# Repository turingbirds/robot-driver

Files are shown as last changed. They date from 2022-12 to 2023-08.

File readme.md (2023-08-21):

# Robot driver

Heavy duty 12 V servo motor driver with Wifi link

**⚠️ Status: prototype ⚠️**

https://user-images.githubusercontent.com/1014092/205401948-c3db500c-c33b-486b-9b15-0c6e07ba4ee2.mp4

pcb

rear

## Features

- 3 bidirectional motor outputs (motors wired as H-bridge; 6 output channels in total)
- Wireless low-latency interface via UDP
- Battery powered with a 14.4 V Makita power tool battery
- Flexible I/O options for motor position encoders, servo motor drivers, etc.
- Hardware address pins allow multiple devices on a network
- Unity VR interface

## Tech

- ESP32 controller
- BTS7960 driver for each output channel
- Inrush current limiter via low-side series MOSFET

PCB fits the case of a Makita battery charger.

Bill of materials: [CSV](bom.csv)

## Benchmarking

### Motor driver

Supply rail transient response during the demo program (as in the video):

transients

transients2

### Network

Each controller announces its presence by sending a UDP broadcast message containing its hardware address and IP address.

Packets containing control commands can then sent to a specific IP address, based on selecting a hardware address.

#### UDP network benchmarks for uncongested wifi
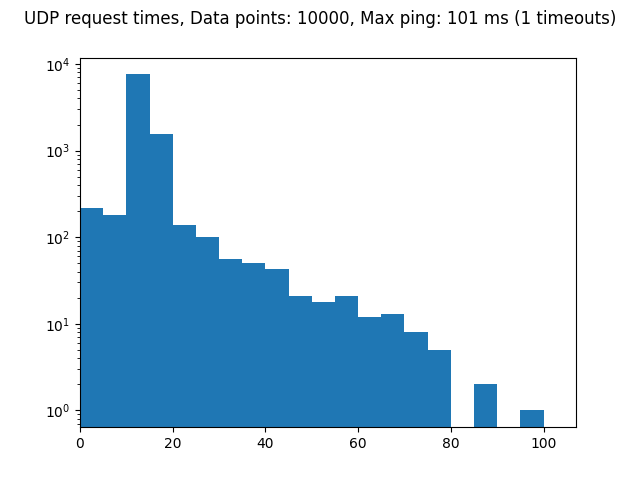
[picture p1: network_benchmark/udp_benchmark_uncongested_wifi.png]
Uncongested wifi


#### UDP network benchmarks for congested wifi
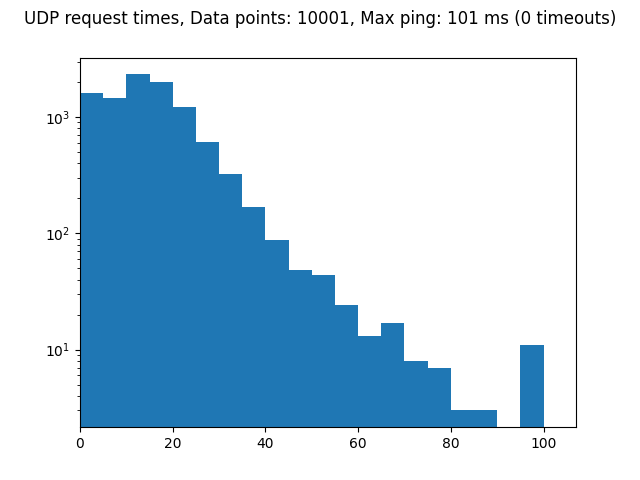
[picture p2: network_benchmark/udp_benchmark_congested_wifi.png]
Congested wifi


## License

[Open source hardware](https://www.oshwa.org/) is hardware for which the design is made publicly available, so that anyone can study, modify, distribute, make, and sell the design or hardware based on that design, subject to the following license conditions.

Hardware licensed under the *CERN Open Hardware Licence Version 2 - Weakly Reciprocal,* a copy of which is included in this repository at [cern_ohl_w_v2.txt](https://github.com/turingbirds/robot-driver/blob/master/cern_ohl_w_v2.txt).

Software licensed under the *Apache License 2.0,* a copy of which is included at [apache_license_2.0.txt](https://github.com/turingbirds/robot-driver/blob/master/apache_license_2.0.txt).

## Credits

This project was co-produced by V2_ Lab for the Unstable Media as part of the Winter Sessions art and technology residencies. ♥️

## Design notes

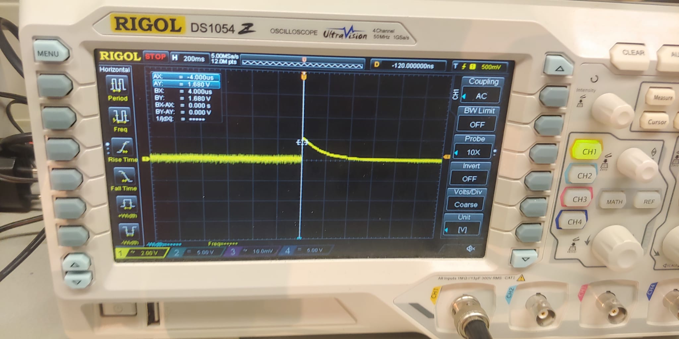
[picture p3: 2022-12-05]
doc/transients2.jpg

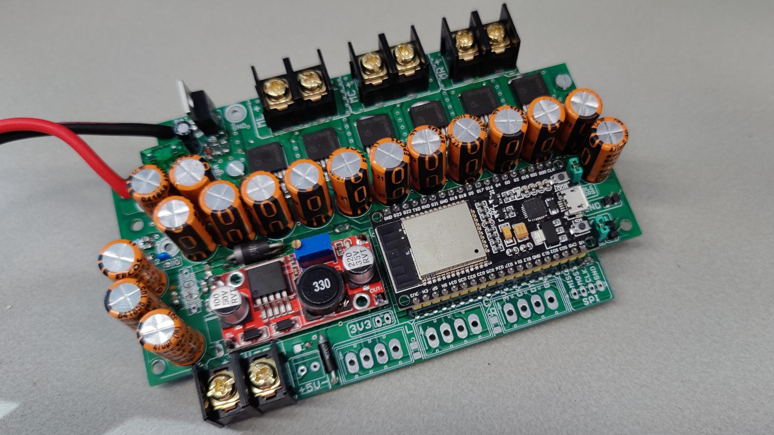
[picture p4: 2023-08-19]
doc/pcb.jpeg

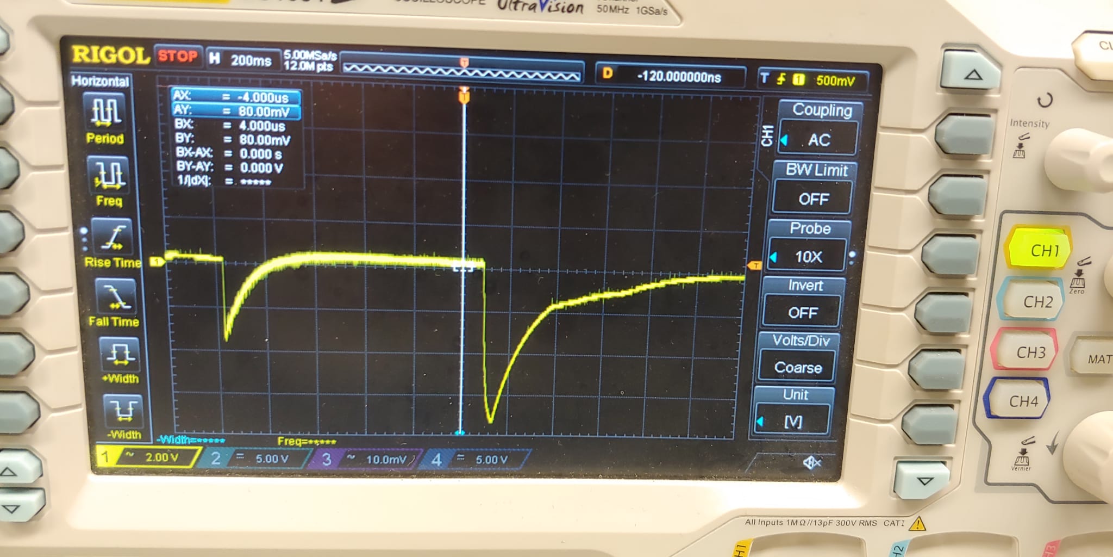
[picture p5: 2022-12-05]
doc/transients.jpg

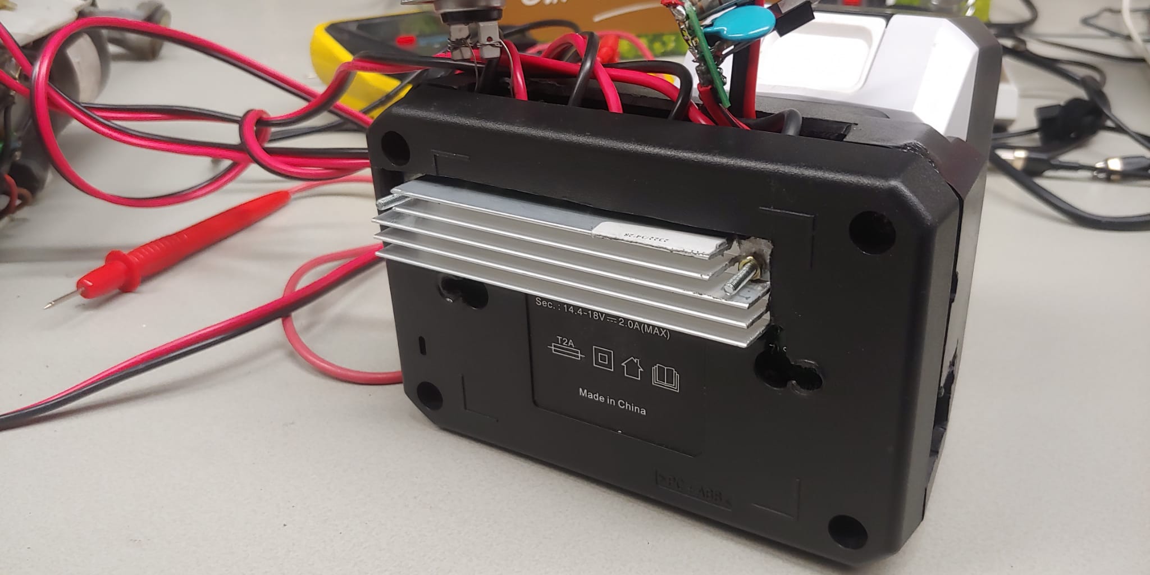
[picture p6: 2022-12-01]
doc/rear.jpeg

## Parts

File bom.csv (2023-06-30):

Qty | Identifier | Description | Value | Package | Price/1 | Price (tot)
6 | R1, R2, R3, R4, R5, R6 | Resistor 0 Ohm |  | 1206 | 0.05
8 | R7, R8, R9, R10, R11, R12, R13, R17 | Resistor 5k Ohm |  | 1206 | 0.05
1 | R14 | Resistor 100k Ohm |  | 1206 | 0.05
2 | R15, R19 | Resistor 100 Ohm 1 W |  | through-hole | 0.25
1 | R16 | Resistor 10k Ohm |  | 1206 | 0.05
1 | R18 | Resistor 22k Ohm |  | 1206 | 0.05
1 | R20 | Resistor 1.2k Ohm |  | 1206 | 0.05
1 | C41 | Electrolytic capacitor | 1 uF, 63V | through-hole, E2.5-6 | 0.25
2 | C1, C44 | Ceramic capacitor | 10 nF, 63 V | through-hole | 0.25
14 | C2, C3, C4, C5, C7, C8, C11, C12, C13, C16, C17, C19, C21, C24, C35, C36, C43 | Electrolytic capacitor | 470 uF, 35 V | through-hole, E5-10.5 | 0.68 | 9.47
23 | C6, C9, C10, C14, C15, C18, C22, C23, C25, C26, C27, C28, C29, C30, C31, C32, C33, C34, C37, C38, C39, C40, C42 | Ceramic capacitor (MLCC) | 100 nF, 25 V | 1206 | 0.05
1 | L1 | EMI suppression inductor (optional)
1 | D1 | 5V6 zener diode | 1N5339 | DO41 | 0.3 | 0.3
1 | D2, D6 | Schottky diode |  | DO15-12
1 | D3 | Schottky diode |  | DO214
2 | D4, D7 | TVS diode | P6KE22A | DO41-7.6 | 0.49 | 0.98
1 | SV6 | IDC header 4-pin
3 | SV7, SV8, SV9 | Screw terminals 4 mm pitch |  |  | 0.12 | 0.36
4 | X1, X6, X7, X8 | Screw terminals 10 mm pitch |  |  | 0.18 | 0.72
1 |  | jumper
3 | JP1, JP2, JP3 | IDC header 2-pin
1 |  | Socket for ESP32 (2x 19 pin female IDC)
 | J6 | Header (optional)
1 | IC2 | ESP32-DEVKIT |  |  | 5 | 5
1 | Q1 | IRLB8743 n-MOSFET |  | TO220 | 3.92 | 3.92
6 | IC3, IC4, IC5, IC6, IC7, IC8 | BTS7960B |  | TO263-7 | 1.44 | 8.62
1 | SV1 | 5V buck converter |  |  | 0.8 | 0.8
1 |  | Heatsink 20x108 mm |  |  | 0.75 | 0.75
1 |  | Thermal pad 20x108 mm |  |  | 2.33 | 2.33
1 |  | 5V DC fan 20 or 25 mm (optional)
1 | F2 | Mini car fuse + holder |  |  | 0.15 | 0.15
1 |  | Enclosure

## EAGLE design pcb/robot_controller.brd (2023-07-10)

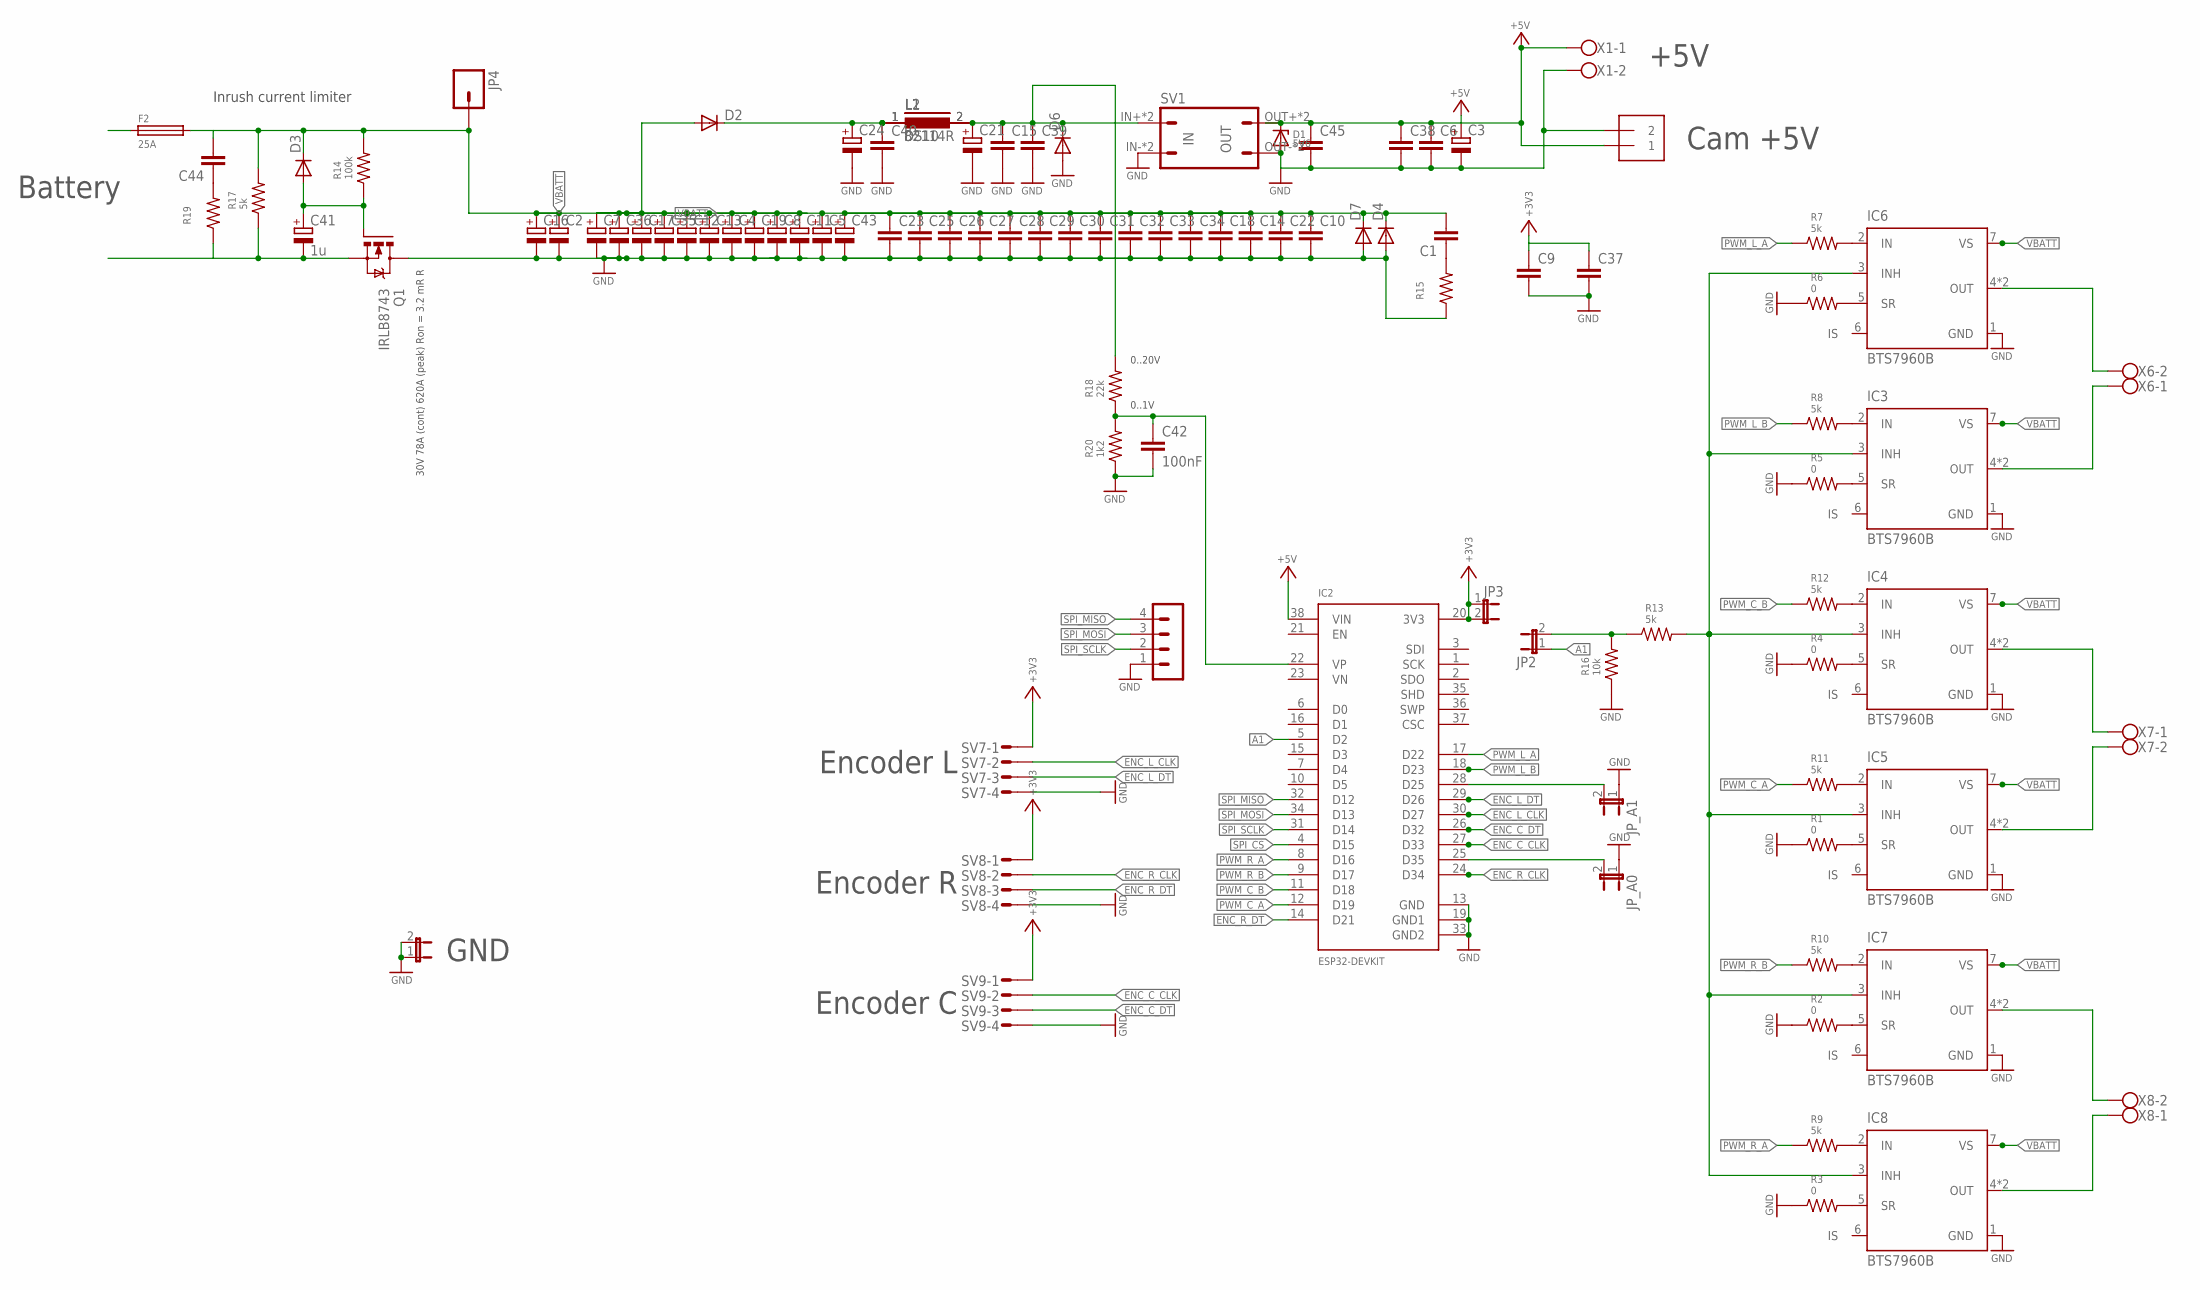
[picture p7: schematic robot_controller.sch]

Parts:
C1: C-EU025-025X050; C025-025X050
C2, C3, C4, C5, C7, C8, C11, C12, C13, C16, C17, C19, C21, C24, C35, C36, C43: CPOL-EUE5-10.5; E5-10,5
C6, C9, C10, C14, C15, C18, C22, C23, C25, C26, C27, C28, C29, C30, C31, C32, C33, C34, C37, C38, C39, C40, C45: C-EUC1206; C1206
C41: 1u; E2,5-6
C42: 100nF; C1206
C44: C-EU050-030X075; C050-030X075
D1: 5V6; DO41Z10
D2, D6: DIODE-DO15-12; DO15-12
D3: DIODE-DO-214AC; DO-214AC
D4, D7: DIODE-DO41-7.6; DO41-7.6
F2: 25A; SHK20L
IC2: ESP32-DEVKIT; DEVKIT-V1-NOHOLES
IC3, IC4, IC5, IC6, IC7, IC8: BTS7960B; P-TO263-7-1
J6: 1X2-3.5MM; 3.5MMTERM
JP1, JP2, JP3: JP1E; JP1
JP4: M01PTH_LONGPAD; 1X01_LONGPAD
JP_A0, JP_A1: JP1E; JP1
L1: 82114R
L2: DS10
Q1: IRLB8743; TO220BV
R1, R2, R3, R4, R5, R6: 0; R1206
R7, R8, R9, R10, R11, R12, R13, R17: 5k; R1206
R14: 100k; R1206
R15: R-US_0411/3V; 0411V
R16: 10k; R1206
R18: 22k; R1206
R19: R-US_0617/5V; 0617V
R20: 1k2; R1206
SV1: MA04-1SMALL; MA04-2
SV6: MA04-1
SV7, SV8, SV9: MT6-4
X1, X6, X7, X8: W239-302

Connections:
+3V3: C9.1, C37.1, IC2.20 (3V3), JP3.1, JP3.2, SV7.1, SV8.1, SV9.1
+5V: C3.+, C6.1, C38.1, C45.1, D1.C, IC2.38 (VIN), J6.1, SV1.OUT+, SV1.OUT+1 (OUT+), X1.1
A1: IC2.5 (D2), JP2.1
ENC_C_CLK: IC2.27 (D33), SV9.2
ENC_C_DT: IC2.26 (D32), SV9.3
ENC_L_CLK: IC2.30 (D27), SV7.2
ENC_L_DT: IC2.29 (D26), SV7.3
ENC_R_CLK: IC2.24 (D34), SV8.2
ENC_R_DT: IC2.14 (D21), SV8.3
GND: C2.-, C3.-, C4.-, C5.-, C6.2, C7.-, C8.-, C9.2, C10.2, C11.-, C12.-, C13.-, C14.2, C15.2, C16.-, C17.-, C18.2, C19.-, C21.-, C22.2, C23.2, C24.-, C25.2, C26.2, C27.2, C28.2, C29.2, C30.2, C31.2, C32.2, C33.2, C34.2, C35.-, C36.-, C37.2, C38.2, C39.2, C40.2, C42.2, C43.-, C45.2, D1.A, D4.A, D6.A, D7.A, IC2.13 (GND), IC2.19 (GND1), IC2.33 (GND2), IC3.1 (GND), IC4.1 (GND), IC5.1 (GND), IC6.1 (GND), IC7.1 (GND), IC8.1 (GND), J6.2, JP1.1, JP1.2, JP_A0.1, JP_A1.1, Q1.D, R1.1, R2.1, R3.1, R4.1, R5.1, R6.1, R15.1, R16.1, R20.1, SV1.IN-, SV1.IN-1 (IN-), SV1.OUT-, SV1.OUT-1 (OUT-), SV6.1, SV7.4, SV8.4, SV9.4, X1.2
unnamed: C24.+, C40.1, D2.C, L1.1, L2.1
unnamed: IC7.4 (OUT), IC7.8 (OUT), X8.2
unnamed: IC7.5 (SR), R2.2
unnamed: IC8.4 (OUT), IC8.8 (OUT), X8.1
unnamed: IC5.4 (OUT), IC5.8 (OUT), X7.2
unnamed: IC4.4 (OUT), IC4.8 (OUT), X7.1
unnamed: F2.1A (1), F2.1B (1)
unnamed: IC2.28 (D25), JP_A1.2
unnamed: IC3.4 (OUT), IC3.8 (OUT), X6.1
unnamed: IC6.4 (OUT), IC6.8 (OUT), X6.2
unnamed: IC5.5 (SR), R1.2
unnamed: IC8.5 (SR), R3.2
unnamed: IC4.5 (SR), R4.2
unnamed: C15.1, C21.+, C39.1, D6.C, L1.2, L2.2, R18.2, SV1.IN+, SV1.IN+1 (IN+)
unnamed: IC3.5 (SR), R5.2
unnamed: IC6.5 (SR), R6.2
unnamed: IC3.3 (INH), IC4.3 (INH), IC5.3 (INH), IC6.3 (INH), IC7.3 (INH), IC8.3 (INH), R13.2
unnamed: IC6.2 (IN), R7.2
unnamed: IC4.2 (IN), R12.2
unnamed: IC5.2 (IN), R11.2
unnamed: IC7.2 (IN), R10.2
unnamed: IC8.2 (IN), R9.2
unnamed: IC3.2 (IN), R8.2
unnamed: C1.1, R15.2
unnamed: JP2.2, R13.1, R16.2
unnamed: IC2.25 (D35), JP_A0.2
unnamed: C41.+, D3.A, Q1.G, R14.1
unnamed: C41.-, Q1.S, R17.1, R19.1
unnamed: C42.1, IC2.22 (VP), R18.1, R20.2
unnamed: C44.1, R19.2
PWM_C_A: IC2.12 (D19), R11.1
PWM_C_B: IC2.11 (D18), R12.1
PWM_L_A: IC2.17 (D22), R7.1
PWM_L_B: IC2.18 (D23), R8.1
PWM_R_A: IC2.8 (D16), R9.1
PWM_R_B: IC2.9 (D17), R10.1
SPI_CS: IC2.4 (D15)
SPI_MISO: IC2.32 (D12), SV6.4
SPI_MOSI: IC2.34 (D13), SV6.3
SPI_SCLK: IC2.31 (D14), SV6.2
VBATT: C1.2, C2.+, C4.+, C5.+, C7.+, C8.+, C10.1, C11.+, C12.+, C13.+, C14.1, C16.+, C17.+, C18.1, C19.+, C22.1, C23.1, C25.1, C26.1, C27.1, C28.1, C29.1, C30.1, C31.1, C32.1, C33.1, C34.1, C35.+, C36.+, C43.+, C44.2, D2.A, D3.C, D4.C, D7.C, F2.2A (2), F2.2B (2), IC3.7 (VS), IC4.7 (VS), IC5.7 (VS), IC6.7 (VS), IC7.7 (VS), IC8.7 (VS), JP4.1, R14.2, R17.2

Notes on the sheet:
GND
Battery
Encoder L
Encoder R
Encoder C
Cam +5V
+5V
Inrush current limiter
30V 78A (cont) 620A (peak) Ron = 3.2 mR R
0..20V
0..1V

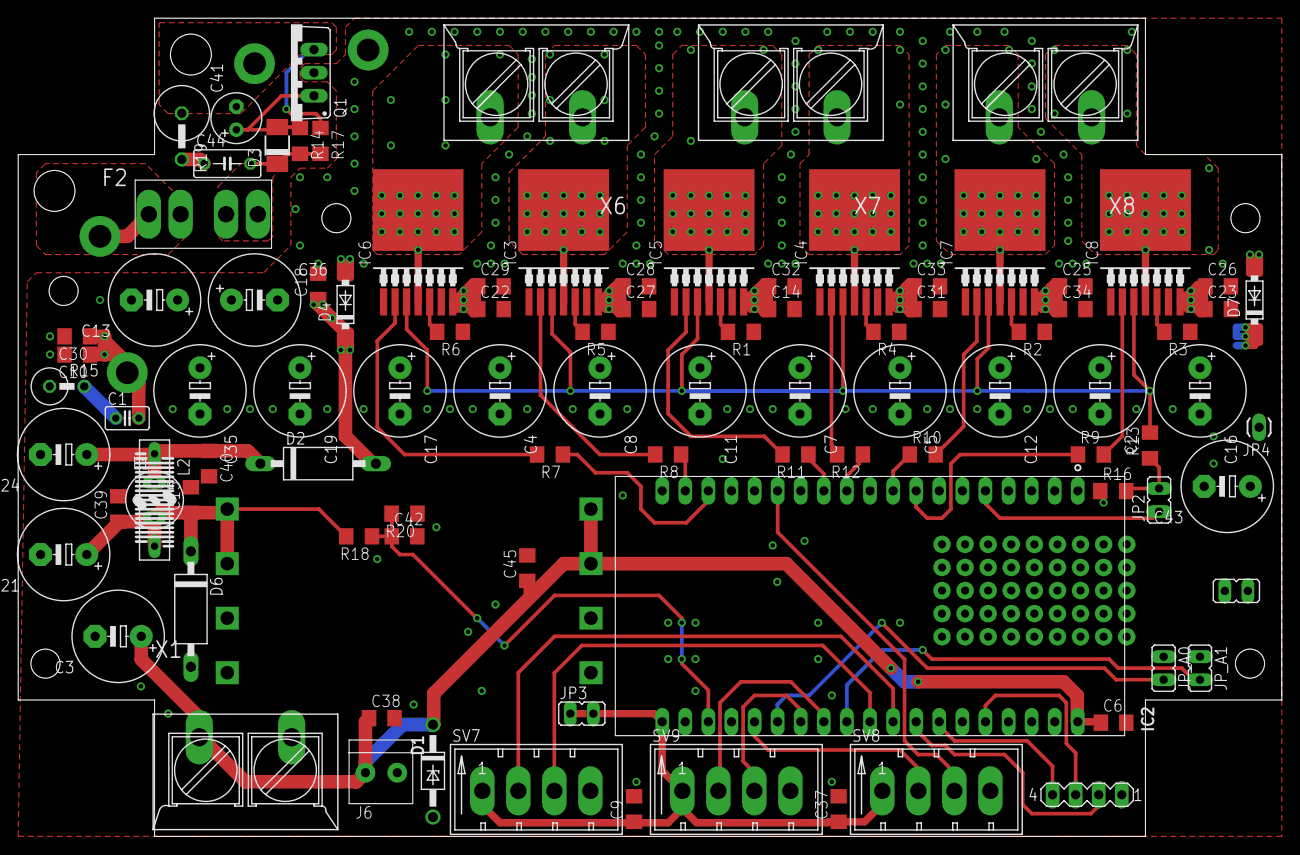
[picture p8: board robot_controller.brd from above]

Board: 2 copper layers, 139.0 x 90.0 mm, 97 parts (0 on the bottom side), 50 nets.

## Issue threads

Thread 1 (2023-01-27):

Add address selection jumpers/switches

turingbirds, 2023-01-27:
Add a feature to allow setting a unique address for each controller using a set of jumpers or switches on the PCB. This makes it easy to use multiple separate controllers at the same time without interference.

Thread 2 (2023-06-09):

Add timing benchmarks

turingbirds, 2023-06-09:
Work in progress.

[esp32_http_server_ping_benchmarks.zip](https://github.com/turingbirds/robot-driver/files/11710532/esp32_http_server_ping_benchmarks.zip)

turingbirds, 2023-06-11:
# HTTP request, uncongested wifi

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

# HTTP request, congested wifi

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

# UDP packet, uncongested wifi

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

# UDP packet, congested wifi

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

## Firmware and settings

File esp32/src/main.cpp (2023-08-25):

/*

Robot controller
----------------

https://github.com/turingbirds/robot-driver

Copyright 2023
Apache License 2.0

*/


/*
 * Serial debugging
**/

// warning!! Enabling serial debug will increase response latency
// set to 1 for on, 0 for off.
#define SERIAL_DEBUG 1
#define SERIAL_DEBUG_DETAILED 0

// broadcast our hardware and IP address over UDP?
#define UDP_BROADCAST 1

#include <esp_task_wdt.h>


/*
 * Wifi
**/

#define WIFI_SSID "wifi ssid"
#define WIFI_PSK  "wifi password"

#include <Esp.h>
#include "esp_system.h"
#include "esp_sleep.h"

#include <WiFi.h>
#include <ArduinoJson.h>
#include "AsyncUDP.h"


// demo mode: no wifi and MQTT, just pulse motors one after the other
#define DEMO_MODE 0
#define DEMO_MODE_ADC_READING 0

// use feedback encoders/servo mode for main motors
#define USE_ENCODERS 0

#define MEASURE_MOTOR_ABSOLUTE_ANGLE 1

// control small "normal" PWM servo motors (pins shared with encoder inputs--select only one at a time)
#define AUX_SERVO_CONTROLLER 1

#define MIN(x, y) ((x)<(y)?(x):(y))
#define MAX(x, y) ((x)>(y)?(x):(y))

// ----------------------------------------------------------------------------
// definitions

#define ADDRESS_SELECT_A0_PIN 35
#define ADDRESS_SELECT_A1_PIN 25

volatile size_t hardware_address = 0;

#define PWM_RESOLUTION 8
#define PWM_FREQ  25000

#define PWM_L_PIN_A 22
#define PWM_L_PIN_B 23
#define PWM_R_PIN_A 19
#define PWM_R_PIN_B 18
#define PWM_C_PIN_A 17
#define PWM_C_PIN_B 16

#define PWM_EN_PIN 2

#define MOTOR_L_PWM_CHANNEL_A 6
#define MOTOR_L_PWM_CHANNEL_B 7
#define MOTOR_R_PWM_CHANNEL_A 2
#define MOTOR_R_PWM_CHANNEL_B 3
#define MOTOR_C_PWM_CHANNEL_A 4
#define MOTOR_C_PWM_CHANNEL_B 5

#if USE_ENCODERS
#define ENCODER_L_CLK_PIN 27
#define ENCODER_L_DT_PIN 26
#define ENCODER_R_CLK_PIN 34
#define ENCODER_R_DT_PIN 21
#define ENCODER_C_CLK_PIN 33
#define ENCODER_C_DT_PIN 32
#endif

#if MEASURE_MOTOR_ABSOLUTE_ANGLE
#define MOTOR_L_ZERO_SWITCH_PIN 26
#define MOTOR_R_ZERO_SWITCH_PIN 34
#endif

#if AUX_SERVO_CONTROLLER
#define AUX_SERVO_PWM_FREQ     50
#define AUX_SERVO_PWM_RESOLUTION  8

#define AUX_SERVO_1_PIN 21
#define AUX_SERVO_2_PIN 33

#define AUX_SERVO_PWM_CHANNEL_1 0
#define AUX_SERVO_PWM_CHANNEL_2 1
#endif

#define BAT_VOLT_ADC_PIN 36

const unsigned int min_dutycycle = 30;  // allow transistor to turn fully on before turning it off on heavy loads (transistor spends too much time in linear range below this value)
const unsigned int max_dutycycle = 211;  // 14.4V supply for a 12V motor -> 83% max duty = 211/255. In the future this could be made dependent on measured battery voltage

// 3 seconds WDT
#define WDT_TIMEOUT 3

#if AUX_SERVO_CONTROLLER
#include <ESP32Servo.h>
#endif

#if !DEMO_MODE
WiFiClient espClient;
AsyncUDP udp;

volatile unsigned long prev_millis = 0;
const unsigned long WIFI_RECONNECT_INTERVAL = 5000; // in milliseconds

unsigned int udp_comms_timeout = 500; // timeout in milliseconds -- stop robot if no packets received for this interval or more
unsigned int udp_time_since_last_packet = 0;
#endif

// ----------------------------------------------------------------------------
// Global state

#if DEMO_MODE
volatile uint8_t foo = 0;
volatile uint8_t motor_idx = 0;
#endif

volatile unsigned int message_counter = 0;

volatile unsigned int frame = 0;

volatile uint32_t serial_delay_counter = 0;
// volatile uint32_t serial_delay_counter2 = 0;
volatile uint32_t bat_volt_adc_raw = 0;
volatile float bat_volt_adc_corrected = -1.;

volatile int vel_L = 0;
volatile int vel_R = 0;
volatile int vel_C = 0;

volatile unsigned int enable_L = 1;   // set to 0 to disable motor
volatile unsigned int enable_R = 1;   // set to 0 to disable motor

volatile unsigned int stop_motor_L_at_zero = 0; // set to 1 to activate
volatile unsigned int stop_motor_R_at_zero = 0; // set to 1 to activate

#if AUX_SERVO_CONTROLLER
// initial servo positions
volatile unsigned int aux_pos_1 = 90;
volatile unsigned int aux_pos_2 = 90;

const unsigned int MAX_AUX_POS_1 = 140;
const unsigned int MIN_AUX_POS_1 = 60;

Servo aux_servo_1;
Servo aux_servo_2;
#endif



//
// void IRAM_ATTR MOTOR_L_PIN_CHANGE_ISR() {
// 	if (stop_motor_L_at_zero) {
// 		enable_L = 0;
// 	}
// }
//
// void IRAM_ATTR MOTOR_R_PIN_CHANGE_ISR() {
// 	if (stop_motor_R_at_zero) {
// 		enable_R = 0;
// 	}
// }




void init_udp_listener() {
	if (udp.listen(1234)) {
		udp.onPacket([](AsyncUDPPacket packet) {

#if SERIAL_DEBUG
			Serial.print("[host -> esp32] UDP Packet Type: ");
			Serial.print(packet.isBroadcast() ? "Broadcast" : packet.isMulticast() ? "Multicast" : "Unicast");
			Serial.print(", From: ");
			Serial.print(packet.remoteIP());
			Serial.print(":");
			Serial.print(packet.remotePort());
			Serial.print(", To: ");
			Serial.print(packet.localIP());
			Serial.print(":");
			Serial.print(packet.localPort());
			Serial.print(", Length: ");
			Serial.print(packet.length()); //dlzka packetu
			Serial.print(", Data: ");
			Serial.write(packet.data(), packet.length());
			Serial.println();
#endif

			if (packet.isBroadcast()) return;

			// reset packet timeout
			udp_time_since_last_packet = 0;

			String data_as_string = (const char*)packet.data();
			DynamicJsonDocument doc(1024);
			deserializeJson(doc, data_as_string);
#if SERIAL_DEBUG
			// Serial.write("[[[]]]%f]]", doc["vel_L"]);


						// message_counter += 1;

				    // char s[256];
			//			sprintf(s, "{\"vel_L\": \"%d\", \"vel_C\": \"%d\", \"vel_R\": \"%d\", \"aux_pos_1\": \"%d\", \"aux_pos_2\": \"%d\", \"cnt\": \"%d\", \"battery_voltage\": \"%f\"}\0", vel_L, vel_C, vel_R, aux_pos_1, aux_pos_2, message_counter, bat_volt_adc_corrected);
						// sprintf(s, "{\"vel_L\": \"%d\", \"vel_C\": \"%d\", \"vel_R\": \"%d\", \"aux_pos_1\": \"%d\", \"aux_pos_2\": \"%d\", \"cnt\": \"%d\", \"battery_voltage\": \"%f\"}\0", vel_L, vel_C, vel_R, aux_pos_1, aux_pos_2, message_counter, bat_volt_adc_corrected);



#endif
			vel_L = doc["vel_L"];
			vel_C = doc["vel_C"];
			vel_R = doc["vel_R"];
			stop_motor_L_at_zero = doc["stop_motor_L_at_zero"];
			stop_motor_R_at_zero = doc["stop_motor_R_at_zero"];
			if (doc["enable_R"]) {
				enable_R = 1;
			}
			if (doc["enable_L"]) {
				enable_L = 1;
			}
#if AUX_SERVO_CONTROLLER
			unsigned int aux_pos_1_new = doc["aux_pos_1"];
			aux_pos_1_new = MIN(MAX_AUX_POS_1, aux_pos_1_new);
			aux_pos_1_new = MAX(MIN_AUX_POS_1, aux_pos_1_new);
			aux_pos_1 = aux_pos_1_new;
			aux_pos_2 = doc["aux_pos_2"];
#endif

			// packet.printf("[esp32 -> host] received %u bytes of data", packet.length());
			packet.printf("{\"battery_voltage\": %f, \"free_heap\": %d, \"sw_L\": %d, \"sw_R\": %d}", bat_volt_adc_corrected, ESP.getFreeHeap(),
			digitalRead(MOTOR_L_ZERO_SWITCH_PIN), digitalRead(MOTOR_R_ZERO_SWITCH_PIN));
		});
	}
}

void init_address_select() {
	pinMode(ADDRESS_SELECT_A0_PIN, INPUT_PULLUP);  // Set the pin as input
	pinMode(ADDRESS_SELECT_A1_PIN, INPUT_PULLUP);  // Set the pin as input
}

void read_address_select() {
	const size_t A_0 = digitalRead(ADDRESS_SELECT_A0_PIN);
	const size_t A_1 = digitalRead(ADDRESS_SELECT_A1_PIN);
	hardware_address = (1 - A_0) | ((1 - A_1) << 1);
}

void init_motors() {
  ledcSetup(MOTOR_L_PWM_CHANNEL_A, PWM_FREQ, PWM_RESOLUTION);
  ledcSetup(MOTOR_L_PWM_CHANNEL_B, PWM_FREQ, PWM_RESOLUTION);
  ledcSetup(MOTOR_R_PWM_CHANNEL_A, PWM_FREQ, PWM_RESOLUTION);
  ledcSetup(MOTOR_R_PWM_CHANNEL_B, PWM_FREQ, PWM_RESOLUTION);
  ledcSetup(MOTOR_C_PWM_CHANNEL_A, PWM_FREQ, PWM_RESOLUTION);
  ledcSetup(MOTOR_C_PWM_CHANNEL_B, PWM_FREQ, PWM_RESOLUTION);

  ledcAttachPin(PWM_L_PIN_A, MOTOR_L_PWM_CHANNEL_A);
  ledcAttachPin(PWM_L_PIN_B, MOTOR_L_PWM_CHANNEL_B);
  ledcAttachPin(PWM_R_PIN_A, MOTOR_R_PWM_CHANNEL_A);
  ledcAttachPin(PWM_R_PIN_B, MOTOR_R_PWM_CHANNEL_B);
  ledcAttachPin(PWM_C_PIN_A, MOTOR_C_PWM_CHANNEL_A);
  ledcAttachPin(PWM_C_PIN_B, MOTOR_C_PWM_CHANNEL_B);

  // enable
  pinMode(PWM_EN_PIN, OUTPUT);
  digitalWrite(PWM_EN_PIN, HIGH);
}

void setup() {
#if SERIAL_DEBUG
  	delay(2000);
  	Serial.begin(115200);

  	Serial.println("Setting up WDT");
  	esp_task_wdt_init(WDT_TIMEOUT, true);
  	esp_task_wdt_add(NULL);

  	// Connect to WiFi
  	Serial.println("Setting up WiFi");
#endif
		init_address_select();
		read_address_select();

		WiFi.setSleep(false);
	  WiFi.begin(WIFI_SSID, WIFI_PSK);
	  while (WiFi.status() != WL_CONNECTED) {
			esp_task_wdt_reset();
	    Serial.print(".");
	    delay(500);
	  }
	  Serial.print("Connected. IP=");
	  Serial.println(WiFi.localIP());
		WiFi.setSleep(false);
		Serial.print("CPU frequency: ");
		Serial.println(getCpuFrequencyMhz());

		// init ADC
	  adcAttachPin(BAT_VOLT_ADC_PIN);
	  analogSetPinAttenuation(BAT_VOLT_ADC_PIN, ADC_2_5db);    // The input voltage of ADC will be attenuated, extending the range of measurement to up to approx. 1100 mV. (1V input = ADC reading of 3722)

		// initialize and power on the motors
	  init_motors();

	// #if AUX_SERVO_CONTROLLER
	//   ledcSetup(AUX_SERVO_PWM_CHANNEL_1, AUX_SERVO_PWM_FREQ, AUX_SERVO_PWM_RESOLUTION);
	//   ledcSetup(AUX_SERVO_PWM_CHANNEL_2, AUX_SERVO_PWM_FREQ, AUX_SERVO_PWM_RESOLUTION);
	//
	//   ledcAttachPin(AUX_SERVO_1_PIN, AUX_SERVO_PWM_CHANNEL_1);
	//   ledcAttachPin(AUX_SERVO_2_PIN, AUX_SERVO_PWM_CHANNEL_2);
	// #endif

#if AUX_SERVO_CONTROLLER
	  ESP32PWM::allocateTimer(AUX_SERVO_PWM_CHANNEL_1);
	  ESP32PWM::allocateTimer(AUX_SERVO_PWM_CHANNEL_2);
	  aux_servo_1.setPeriodHertz(50); // [Hz]
	  aux_servo_2.setPeriodHertz(50); // [Hz]
	  aux_servo_1.attach(AUX_SERVO_1_PIN, 500, 2400);
	  aux_servo_2.attach(AUX_SERVO_2_PIN, 500, 2400);
#endif

  pinMode(MOTOR_L_ZERO_SWITCH_PIN, INPUT_PULLUP);  // Set the pin as input
	pinMode(MOTOR_R_ZERO_SWITCH_PIN, INPUT_PULLUP);  // Set the pin as input
	//attachInterrupt(MOTOR_L_ZERO_SWITCH_PIN, MOTOR_L_PIN_CHANGE_ISR, RISING);
	//attachInterrupt(MOTOR_R_ZERO_SWITCH_PIN, MOTOR_R_PIN_CHANGE_ISR, RISING);



	init_udp_listener();
}

#if DEMO_MODE
void demo_mode_loop() {
  ++foo;
  if (foo > max_dutycycle) {
    foo = min_dutycycle;
    ++motor_idx;
    if (motor_idx >= 12) {
      motor_idx = 0;
    }

#if DEMO_MODE_ADC_READING5
    bat_volt_adc_raw = analogRead(BAT_VOLT_ADC_PIN);
    const float bat_volt_adc = bat_volt_adc_raw * 0.0067;
    const float bat_volt_adc_corrected = bat_volt_adc + (20. - bat_volt_adc) / 20.; // some ad-hoc correction of the horrible ADC nonlinearity

    Serial.print(bat_volt_adc_raw);
    Serial.println();
    Serial.printf("%f\n", bat_volt_adc_corrected);
#endif
  }

  // one motor after the other
  if (motor_idx == 0) {
    ledcWrite(MOTOR_L_PWM_CHANNEL_A, foo);
    ledcWrite(MOTOR_L_PWM_CHANNEL_B, 0);
    ledcWrite(MOTOR_R_PWM_CHANNEL_A, 0);
    ledcWrite(MOTOR_R_PWM_CHANNEL_B, 0);
    ledcWrite(MOTOR_C_PWM_CHANNEL_A, 0);
    ledcWrite(MOTOR_C_PWM_CHANNEL_B, 0);
  }
  else if (motor_idx == 1) {
    ledcWrite(MOTOR_L_PWM_CHANNEL_A, 0);
    ledcWrite(MOTOR_L_PWM_CHANNEL_B, 0);
    ledcWrite(MOTOR_R_PWM_CHANNEL_A, foo);
    ledcWrite(MOTOR_R_PWM_CHANNEL_B, 0);
    ledcWrite(MOTOR_C_PWM_CHANNEL_A, 0);
    ledcWrite(MOTOR_C_PWM_CHANNEL_B, 0);
  }
  else if (motor_idx == 2) {
    ledcWrite(MOTOR_L_PWM_CHANNEL_A, 0);
    ledcWrite(MOTOR_L_PWM_CHANNEL_B, 0);
    ledcWrite(MOTOR_R_PWM_CHANNEL_A, 0);
    ledcWrite(MOTOR_R_PWM_CHANNEL_B, 0);
    ledcWrite(MOTOR_C_PWM_CHANNEL_A, foo);
    ledcWrite(MOTOR_C_PWM_CHANNEL_B, 0);
  }
  else if (motor_idx == 3) {
    ledcWrite(MOTOR_L_PWM_CHANNEL_A, 0);
    ledcWrite(MOTOR_L_PWM_CHANNEL_B, foo);
    ledcWrite(MOTOR_R_PWM_CHANNEL_A, 0);
    ledcWrite(MOTOR_R_PWM_CHANNEL_B, 0);
    ledcWrite(MOTOR_C_PWM_CHANNEL_A, 0);
    ledcWrite(MOTOR_C_PWM_CHANNEL_B, 0);
  }
  else if (motor_idx == 4) {
    ledcWrite(MOTOR_L_PWM_CHANNEL_A, 0);
    ledcWrite(MOTOR_L_PWM_CHANNEL_B, 0);
    ledcWrite(MOTOR_R_PWM_CHANNEL_A, 0);
    ledcWrite(MOTOR_R_PWM_CHANNEL_B, foo);
    ledcWrite(MOTOR_C_PWM_CHANNEL_A, 0);
    ledcWrite(MOTOR_C_PWM_CHANNEL_B, 0);
  }
  else if (motor_idx == 5) {
    ledcWrite(MOTOR_L_PWM_CHANNEL_A, 0);
    ledcWrite(MOTOR_L_PWM_CHANNEL_B, 0);
    ledcWrite(MOTOR_R_PWM_CHANNEL_A, 0);
    ledcWrite(MOTOR_R_PWM_CHANNEL_B, 0);
    ledcWrite(MOTOR_C_PWM_CHANNEL_A, 0);
    ledcWrite(MOTOR_C_PWM_CHANNEL_B, foo);
  }
  else if (motor_idx == 6) {
    ledcWrite(MOTOR_L_PWM_CHANNEL_A, 0);
    ledcWrite(MOTOR_L_PWM_CHANNEL_B, foo);
    ledcWrite(MOTOR_R_PWM_CHANNEL_A, 0);
    ledcWrite(MOTOR_R_PWM_CHANNEL_B, foo);
    ledcWrite(MOTOR_C_PWM_CHANNEL_A, 0);
    ledcWrite(MOTOR_C_PWM_CHANNEL_B, foo);
  }
  else if (motor_idx == 7) {
    ledcWrite(MOTOR_L_PWM_CHANNEL_A, foo);
    ledcWrite(MOTOR_L_PWM_CHANNEL_B, 0);
    ledcWrite(MOTOR_R_PWM_CHANNEL_A, foo);
    ledcWrite(MOTOR_R_PWM_CHANNEL_B, 0);
    ledcWrite(MOTOR_C_PWM_CHANNEL_A, foo);
    ledcWrite(MOTOR_C_PWM_CHANNEL_B, 0);
  }
  else if (motor_idx == 8) {
    ledcWrite(MOTOR_L_PWM_CHANNEL_A, 0);
    ledcWrite(MOTOR_L_PWM_CHANNEL_B, max_dutycycle-foo);
    ledcWrite(MOTOR_R_PWM_CHANNEL_A, 0);
    ledcWrite(MOTOR_R_PWM_CHANNEL_B, max_dutycycle-foo);
    ledcWrite(MOTOR_C_PWM_CHANNEL_A, 0);
    ledcWrite(MOTOR_C_PWM_CHANNEL_B, max_dutycycle-foo);
  }
  else if (motor_idx == 9) {
    ledcWrite(MOTOR_L_PWM_CHANNEL_A, max_dutycycle-foo);
    ledcWrite(MOTOR_L_PWM_CHANNEL_B, 0);
    ledcWrite(MOTOR_R_PWM_CHANNEL_A, max_dutycycle-foo);
    ledcWrite(MOTOR_R_PWM_CHANNEL_B, 0);
    ledcWrite(MOTOR_C_PWM_CHANNEL_A, max_dutycycle-foo);
    ledcWrite(MOTOR_C_PWM_CHANNEL_B, 0);
  }
  else if (motor_idx == 10 || motor_idx == 11) {
    ledcWrite(MOTOR_L_PWM_CHANNEL_A, max_dutycycle);
    ledcWrite(MOTOR_L_PWM_CHANNEL_B, 0);
    ledcWrite(MOTOR_R_PWM_CHANNEL_A, max_dutycycle);
    ledcWrite(MOTOR_R_PWM_CHANNEL_B, 0);
    ledcWrite(MOTOR_C_PWM_CHANNEL_A, max_dutycycle);
    ledcWrite(MOTOR_C_PWM_CHANNEL_B, 0);
  }
  delay(10);
}
#endif

volatile float motor_l_zero_switch_pin = 0.;
volatile float motor_r_zero_switch_pin = 0.;

void read_battery_voltage() {
	const float bat_volt_adc_raw = analogRead(BAT_VOLT_ADC_PIN);
	const float bat_volt_adc = bat_volt_adc_raw * 0.0067;
	bat_volt_adc_corrected = bat_volt_adc + (20. - bat_volt_adc) / 20.; // some ad-hoc correction of the horrible ADC nonlinearity
}

void loop() {
	// reset watchdog timer
	esp_task_wdt_reset();
	unsigned long current_millis = millis();

	// update this in loop() so we can change the address without having to reboot
	read_address_select();

	// read out the motor zero-degree indicator pin and stop the motor if necessary
	motor_r_zero_switch_pin = .5 * motor_r_zero_switch_pin + .5 * ((int)digitalRead(MOTOR_R_ZERO_SWITCH_PIN));
	if (stop_motor_R_at_zero && motor_r_zero_switch_pin > .9) {
		enable_R = 0;
	}

	motor_l_zero_switch_pin = .5 * motor_l_zero_switch_pin + .5 * ((int)digitalRead(MOTOR_L_ZERO_SWITCH_PIN));
	if (stop_motor_L_at_zero && motor_l_zero_switch_pin > .9) {
		enable_L = 0;
	}

#if DEMO_MODE
	demo_mode_loop();
	return;

#else

	if (WiFi.status() != WL_CONNECTED) {
		vel_L = 0;
		vel_C = 0;
		vel_R = 0;

		Serial.println("Wifi got disconnected! Attempting to reconnect...");

		WiFi.disconnect();
		WiFi.setSleep(false);
	  WiFi.begin(WIFI_SSID, WIFI_PSK);
	  while (WiFi.status() != WL_CONNECTED) {
			esp_task_wdt_reset();
	    Serial.print(".");
	    delay(500);
	  }
	  Serial.print("Connected. IP=");
	  Serial.println(WiFi.localIP());
		WiFi.setSleep(false);

		udp_time_since_last_packet = 0;
	}

	// network timeout handling
	delay(10); // do not make delay too low (or other code in loop() take too long), otherwise the estimate for udp_time_since_last_packet will be off by too much
	udp_time_since_last_packet += 10;

	if (udp_time_since_last_packet > udp_comms_timeout) {
		vel_L = 0;
		vel_C = 0;
		vel_R = 0;
	}

  // report on battery voltage
	++serial_delay_counter;
	if (serial_delay_counter >= 100) { // every 100 ms
		serial_delay_counter = 0;

#if UDP_BROADCAST
	// broadcast our presence
	char s[80];
	sprintf(s, "Robot A%d, IP: %s", hardware_address, WiFi.localIP().toString().c_str());
	udp.broadcast(s);
#endif

#if SERIAL_DEBUG
		Serial.print("Free heap: ");
		Serial.println(ESP.getFreeHeap());
		Serial.print("IP: ");
		Serial.println(WiFi.localIP());
#if SERIAL_DEBUG_DETAILED
  // enabling this renders everything very, very slow
  Serial.print("vel_R = ");
  Serial.print(vel_R);
  Serial.print(". vel_L = ");
  Serial.print(vel_L);
  Serial.print(", vel_C = ");
  Serial.print(vel_C);
  Serial.println();
#if AUX_SERVO_CONTROLLER
  Serial.print("aux_servo_pos_1 = ");
  Serial.print(aux_pos_1);
  Serial.print(", aux_servo_pos_2 = ");
  Serial.print(aux_pos_2);
  Serial.println();
	Serial.print(", bat_volt_raw = ");
	Serial.print(bat_volt_adc_raw);
	Serial.println();
	Serial.printf("%f\n", bat_volt_adc_corrected);
#endif
#endif
#endif
		read_battery_voltage();
  }

  // set motors
  if (vel_L > 0) {
    ledcWrite(MOTOR_L_PWM_CHANNEL_A, 0);
    ledcWrite(MOTOR_L_PWM_CHANNEL_B, enable_L * vel_L);
  }
  else if (vel_L < 0) {
    ledcWrite(MOTOR_L_PWM_CHANNEL_A, -enable_L * vel_L);
    ledcWrite(MOTOR_L_PWM_CHANNEL_B, 0);
  }
  else {
    ledcWrite(MOTOR_L_PWM_CHANNEL_A, 0);
    ledcWrite(MOTOR_L_PWM_CHANNEL_B, 0);
  }

  if (vel_R > 0) {
    ledcWrite(MOTOR_R_PWM_CHANNEL_A, 0);
    ledcWrite(MOTOR_R_PWM_CHANNEL_B, enable_R * vel_R);
  }
  else if (vel_R < 0) {
    ledcWrite(MOTOR_R_PWM_CHANNEL_A, -enable_R * vel_R);
    ledcWrite(MOTOR_R_PWM_CHANNEL_B, 0);
  }
  else {
    ledcWrite(MOTOR_R_PWM_CHANNEL_A, 0);
    ledcWrite(MOTOR_R_PWM_CHANNEL_B, 0);
  }

  if (vel_C > 0) {
    ledcWrite(MOTOR_C_PWM_CHANNEL_A, 0);
    ledcWrite(MOTOR_C_PWM_CHANNEL_B, vel_C);
  }
  else if (vel_C < 0) {
    ledcWrite(MOTOR_C_PWM_CHANNEL_A, -vel_C);
    ledcWrite(MOTOR_C_PWM_CHANNEL_B, 0);
  }
  else {
    ledcWrite(MOTOR_C_PWM_CHANNEL_A, 0);
    ledcWrite(MOTOR_C_PWM_CHANNEL_B, 0);
  }

#ifdef AUX_SERVO_CONTROLLER
	// set servo controllers
  aux_servo_1.write(aux_pos_1);
  aux_servo_2.write(aux_pos_2);
#endif

#endif
}

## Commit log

2022-12-01 add esp32
2022-12-01 add pcb
    [robot_controller.brd, robot_controller.sch]
2022-12-22 controller reports on battery voltage
2022-12-22 update PCB to v1.1
    [robot_controller.brd, robot_controller.sch]
2022-12-23 add bill of materials
    [bom.csv]
2022-12-31 update PCB and gerbers for v1.1
    [robot_controller.GBL, robot_controller.GBO, robot_controller.GBP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]
2023-01-01 update BOM
    [bom.csv]
2023-01-12 fix drill sizes on PCB
    [robot_controller.GBL, robot_controller.GBS, robot_controller.GTL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]
2023-02-12 add jumpers to the PCB for setting the address
    [robot_controller.brd, robot_controller.sch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]
2023-02-21 add support for controlling small normal servo motors
2023-02-22 fix auxiliary servo motor control
2023-02-26 add support for aux servos
2023-06-30 add ESP32 header to BOM
    [bom.csv]
2023-07-10 add GND and +12V tap points to the controller PCB
    [robot_controller.GBL, robot_controller.GBO, robot_controller.GBP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]
2023-08-19 add pcb photo
2023-08-25 fix pull-up on switches and low-pass filtering
    [main.cpp]
